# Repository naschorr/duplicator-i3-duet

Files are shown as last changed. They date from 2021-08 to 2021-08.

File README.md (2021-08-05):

# duplicator-i3-duet
Complete Duet 3 Mini 5+ based overhaul for the Duplicator i3 family of printers

Note that this repository is a work in progress, so some parts may not be compatible with the printer yet.

## Components
These are the required components for the upgraded printer, each section goes over it's own list of parts, printables, and tools.

- [duet case and mount assembly](assemblies/duet_case_and_mount_assembly.md)
- [extruder assembly](assemblies/extruder_assembly.md)
- [power supply dock and mount assembly](assemblies/power_supply_dock_and_mount_assembly.md)
- [x axis motor assembly](assemblies/x_axis_motor_assembly.md)
- [y axis carriage assembly](assemblies/y_axis_carriage_assembly.md)

## Required Tools
| Tool | Link | Notes |
| ---- | ---- | ----- |
| Terminal Crimper | [Amazon](https://smile.amazon.com/s?k=molex+jst+crimper) | Make sure it can do 26 gauge thru 12 gauge terminals
| Flush Cutter | [Amazon](https://smile.amazon.com/Hakko-CHP-170-Micro-Cutter/dp/B00FZPDG1K/) |
| Wire Stripper | [Amazon](https://smile.amazon.com/s?k=wire+stripper) |
| Power Drill |
| 1/8 Twist Drill Bit | [Amazon](https://smile.amazon.com/s?k=1%2F8+twist+drill) | This is for cleaning up a few 3D printed holes, so low quality is fine
| Heat Gun (or a lighter) | [Amazon](https://smile.amazon.com/s?k=heat+gun) | This is for heating up heatshrink tubing, so a lighter is totally fine
| Screw Driver Set | [Amazon](https://smile.amazon.com/Syntus-Precision-Screwdriver-Electronics-Cellphone/dp/B071PB4RPV) | Must contain a variety of Hex and Philips head drivers

## Wiring
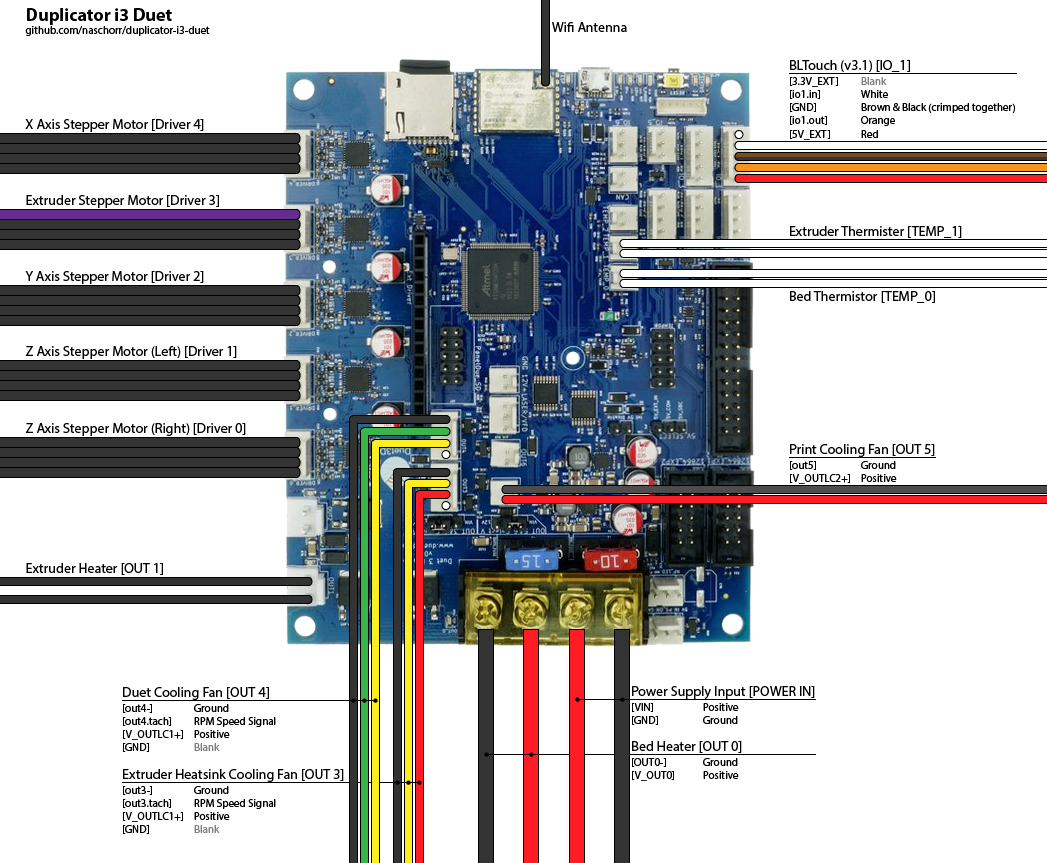
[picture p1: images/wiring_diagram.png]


## SD Card
The `*.g` files inside the [sd_card](sd_card/) directory contain the current state of configuration for the printer. Assuming an identical setup, these files can simply overwrite the data on your Duet's `System` directory.

## Additional Recommended Upgrades & Maintenance
- [Borosilicate Glass Bed](upgrades/borosilicate_glass_bed.md)
- [Z Braces](https://www.thingiverse.com/thing:921948)
- [Bed Levelling Thumbwheels](https://www.thingiverse.com/thing:1917422)
- [GT2 5mm Idler Pulleys](https://smile.amazon.com/gp/product/B01H3F8LUU)

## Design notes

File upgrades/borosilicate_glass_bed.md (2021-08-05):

# Borosilicate Glass Bed Upgrade

Upgrades the existing print surface to include a larger, flatter bed that makes the entire print volume available.

## Required Tools
| Tool | Link | Notes |
| ---- | ---- | ----- |
| Power Drill |
| Countersink Drill Bit | [Amazon](https://smile.amazon.com/gp/product/B0002EVG0C) | The aluminum of the bed is soft, so you can get a cheaper one if desired
| Goo Gone | [Amazon](https://smile.amazon.com/Goo-Gone-Adhesive-Remover-Spray/dp/B00S9YIQMS)  | The spray bottle isn't necessary, but it should make application easier
| Sharp Metal Spatula | | The Duplicator i3 should've already come with one

## Bill of Materials
| Item | Quantity | Link | Notes |
| ---- | --- | ---- | ----- |
| 235mm² Borosilicate Glass Bed | 1 | [Amazon](https://smile.amazon.com/gp/product/B07JKGNB6W)  |
| 200mm² 1mm Silicone Thermal Pad | 1 | [Amazon](https://smile.amazon.com/gp/product/B08YJNDLGM)  |
| M3 25mm Countersunk Machine Screw | 4 | Amazon
| M3 Locknuts | 4 | Amazon |
| Glass Bed Clips | 4 | [Amazon](https://smile.amazon.com/gp/product/B08W8NXMJC)  |

## Assembly
1. Remove the existing print surface, and if necessary scrape away any adhesive with the Goo Gone and a sharp spatula.
2. Remove the heated bed plate from the Y carriage. Making sure to remove the screws, washers, and springs.
3. Use the countersink drill bit to countersink the top of each of the screw holes. The countersink screws should sit very slightly proud of the heated bed's surface. Be careful not to remove too much material as the thin aluminum below the countersink can fail when tightening the screws down.
4. Reassemble the heated build plate
    - Place a M3 countersink screw through one of the bed's holes
    - Place one of the old washers on the screw, against the bottom of the bed
    - Tighten a M3 locknut on the screw until it touches the washer snugly. Don't over torque the nut as it will damage the bed.
    - Repeat for each of the four holes
5. Add a spring and a washer to each of the screws, and then lower the whole assembly back onto the Y carriage. Make sure all of the screws are properly aligned into their holes in the carriage without any binding.
6. Tighten the bed levelling thumbwheels/wingnuts onto each of the protruding screws below the Y carriage.
7. Apply the glass bed clips as necessary near each corner.
8. Update `config.g` to use the appropriate X and Y axis maxima.
9. Manually re-tram the bed, before performing a final mesh bed probe operation (`Control` > `Dashboard` > `Compensation & Calibration` > `Run Mesh Compensation (G29)`).
10. After the probing has completed, you can view the results in the height map viewer (`Control` > `Height Map`), assuming the height map plugin is enabled. Note that height maps must be activated, so that compensation can be applied. If you're using my configuration, then this is done for you.

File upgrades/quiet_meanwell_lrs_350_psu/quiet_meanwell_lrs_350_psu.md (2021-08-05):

# Quiet Meanwell LRS-350-12 Power Supply

Upgrades the default 12v power supply to a Meanwell LRS-350-12, with a larger, quieter fan. Note that this assembly uses the same chassis mount as the plain Meanwell LRS-350 power supply upgrade. This upgrade requires opening up the power supply, so obviously be careful and don't do anything dangerous while you're in there. If you're not comfortable with working around (potentially) charged capacitors then don't attempt this upgrade.

## Bill of Materials
| Item | Quantity | Link | Notes |
| ---- | --- | ---- | ----- |
| Meanwell LRS-350-12 Power Supply  | 1 | [Mouser](https://www.mouser.com/ProductDetail/709-LRS350-12) |
| Noctua NF-A9x14 PWM | 1 | [Amazon](https://smile.amazon.com/gp/product/B009NQM7V2/) | Alternatively, any 92x14mm fan will work here, I just like the performance and quietness of the Noctua.
| 4 Pin to 2 Pin Fan Adapter | 1 | [Amazon](https://smile.amazon.com/s?k=4+pin+to+2+pin+fan+adapter) | The Noctua NF-A4x10 FLX listed in the main bill of materials should come with a 3 pin to 2 pin adapter, which can be cut to allow a 4 pin header to connect. Note that I had to swap the order of the pins in the 2 pin end of the adapter. Alternatively you can purchase a new one.
| M3 6mm Socket Cap Machine Screws  | 4 | Amazon | If you've done the Z brace upgrade, then you likely have enough screws left over from that.
| M4 6mm Socket Cap Machine Screws  | 2 | Amazon | You can salvage these (non socket cap) from the printer's Y axis bearing block during the upgrade.
| M4 Washers | 2 | [Amazon](https://smile.amazon.com/gp/product/B07CG9J4NC) |
| 92mm Fan Filter Mesh | 1 | [Amazon](https://smile.amazon.com/ThreeBulls-Cooler-Filter-Dustproof-Computer/dp/B01N952K7P) | These are 120mm, but they're easier to find, useful elsewhere, and easy to cut to shape.
| Zip tie | 1 | [Amazon](https://smile.amazon.com/AmazonBasics-Multi-Purpose-Cable-Ties-200-Piece/dp/B087MKMSDY)  |

## Required Tools
| Tool | Link | Notes |
| ---- | ---- | ----- |
| Screw Driver Set  | [Amazon](https://smile.amazon.com/Syntus-Precision-Screwdriver-Electronics-Cellphone/dp/B071PB4RPV) | Must contain a variety of Hex and Phillips head drivers

## Printables
All items can be printed with a lower temperature filament, like PLA.
| STL | Quantity | Notes |
| --- | --- | ----- |
| duplicator i3 duet lrs 350 psu 92mm fan case.stl | 1 | This is the new outer case for the power supply, with a mounting solution for a 92x14mm fan.
| duplicator i3 duet lrs 350 psu 92mm fan dock.stl | 1 | This is the revised dock that the power supply (with case) slides into
| duplicator i3 duet lrs 350 psu 92mm fan clip.stl | 4 | These are the clips that screw into the outer case which hold the fan in place

## Assembly
Here's what the almost-completed 92mm fan case assembly should look like, with the fan, filter mesh (not seen), and fan clips installed into the fan case. All that's left to do is to screw the newly printed case and the original metal case together with the four original screws.

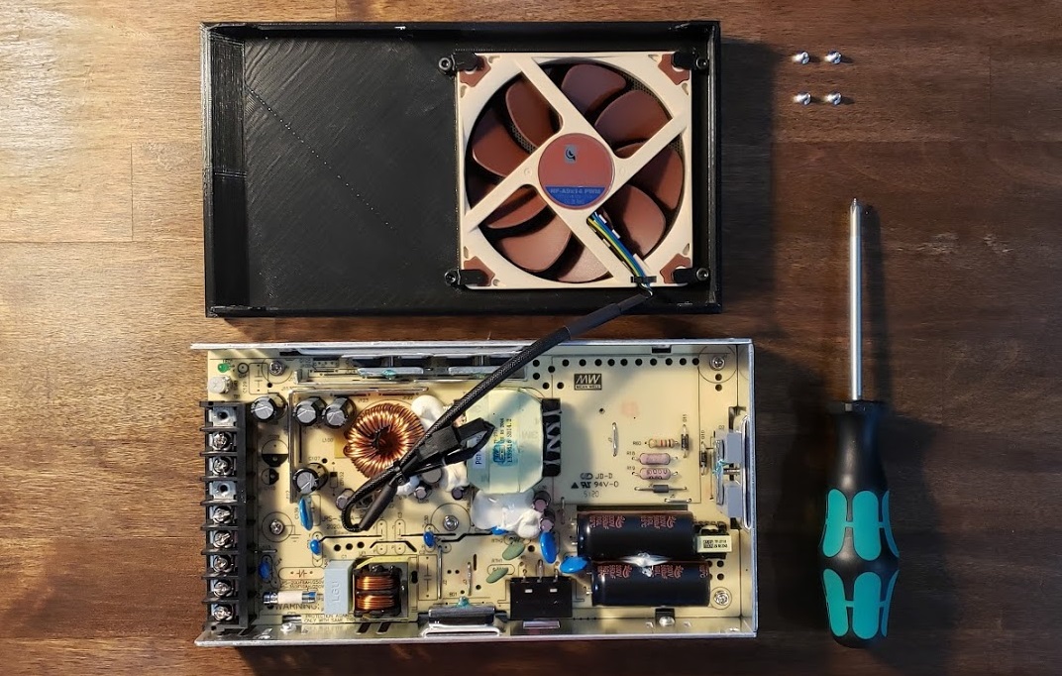
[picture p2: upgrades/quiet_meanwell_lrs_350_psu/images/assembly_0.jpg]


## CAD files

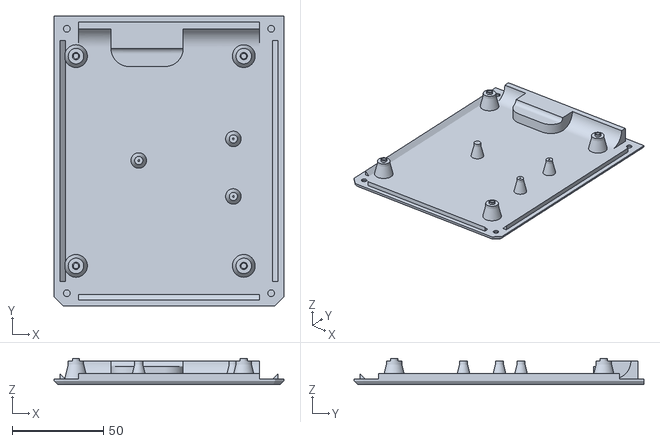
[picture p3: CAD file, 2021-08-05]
stls/duet_case_and_mount_assembly/duplicator i3 duet controller case back panel.stl
126.0 x 159.0 x 14.4

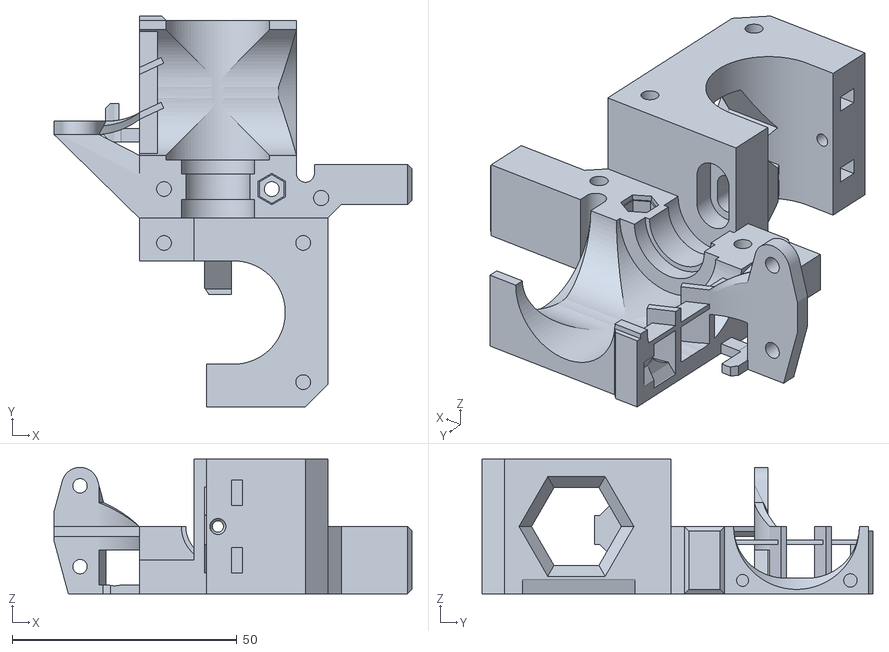
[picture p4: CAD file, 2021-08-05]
stls/extruder_assembly/duplicator i3 duet extruder body bltouch mount.stl
79.7 x 87.0 x 30.0

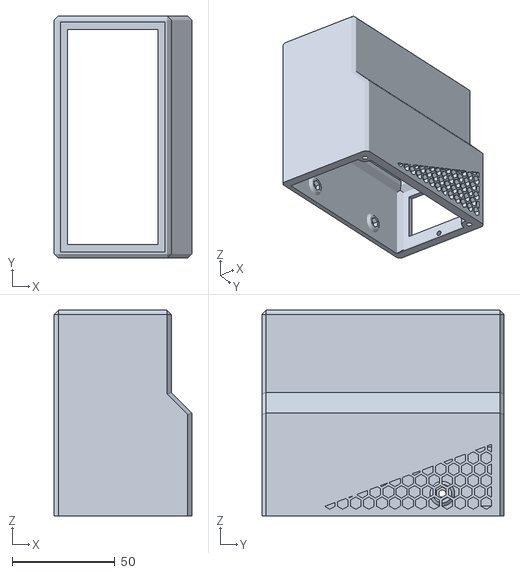
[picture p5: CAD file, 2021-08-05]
stls/power_supply_dock_and_mount_assembly/maker_select/duplicator i3 duet stock psu dock.stl
67.0 x 117.8 x 100.0

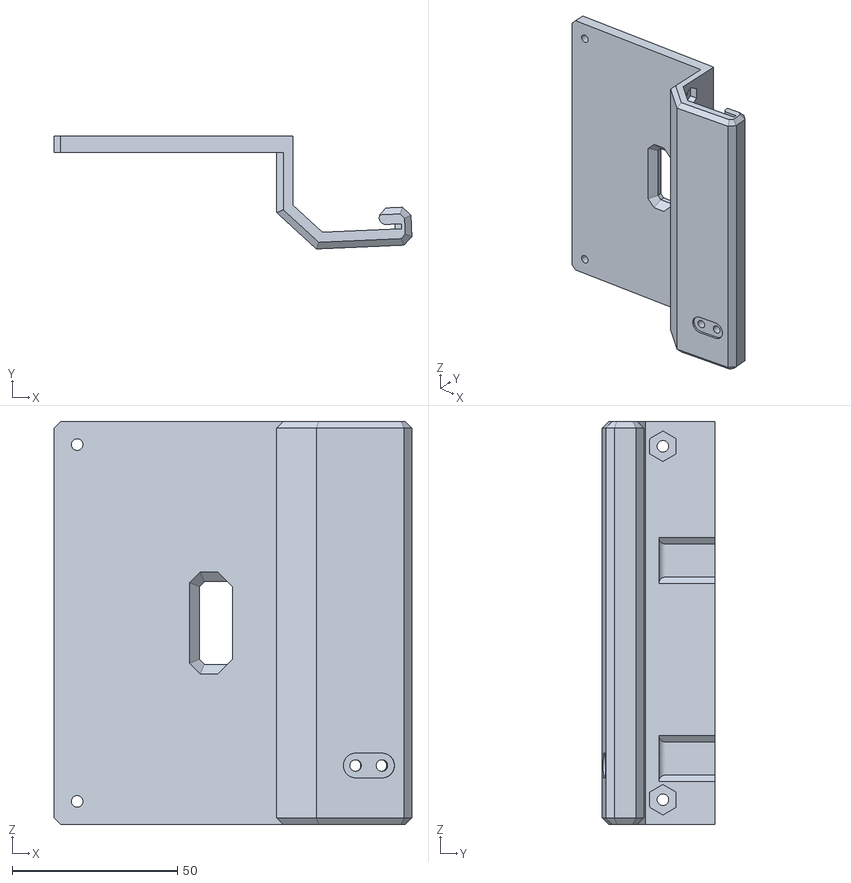
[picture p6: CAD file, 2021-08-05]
stls/power_supply_dock_and_mount_assembly/meanwell_lrs_350/duplicator i3 duet lrs 350 psu chassis mount.stl
108.3 x 34.2 x 122.0

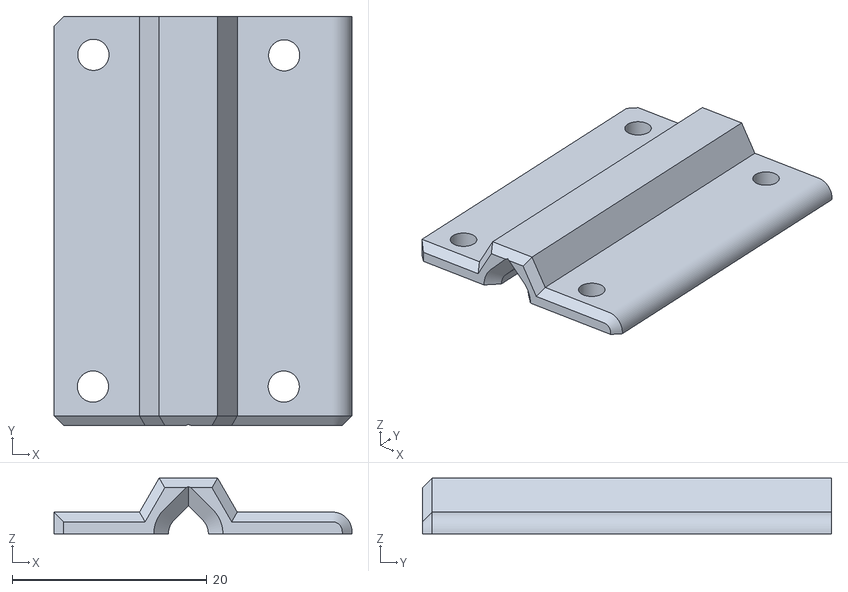
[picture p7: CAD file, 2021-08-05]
stls/x_axis_motor_assembly/duplicator i3 duet x motor ptfe outer clamp.stl
30.6 x 42.0 x 5.75

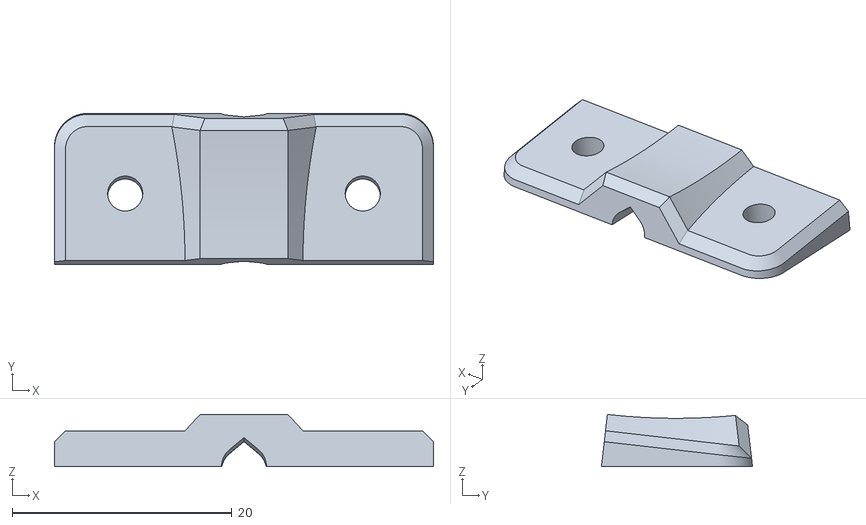
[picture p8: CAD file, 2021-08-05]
stls/y_axis_carriage_assembly/duplicator i3 duet y carriage bearing block ptfe angled clamp.stl
34.5 x 13.8 x 4.75

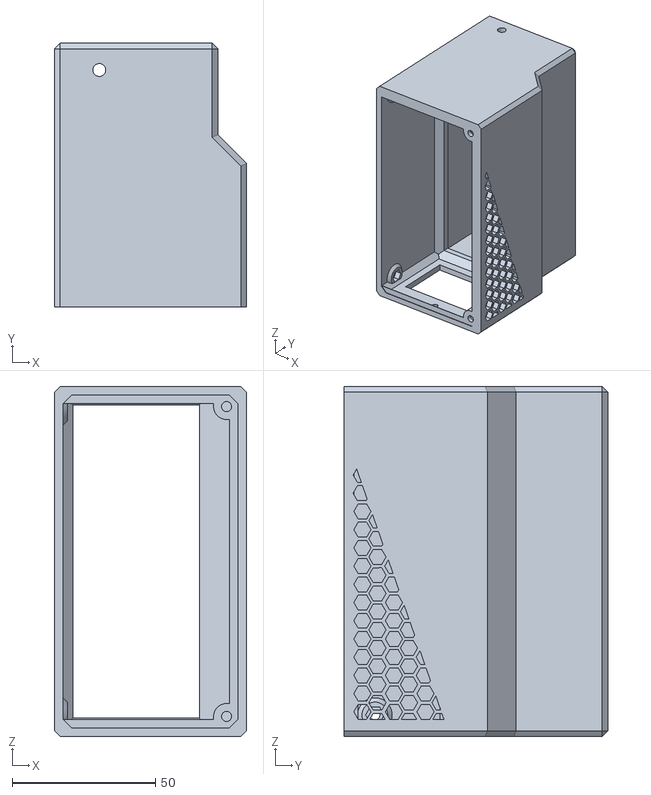
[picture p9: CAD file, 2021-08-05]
upgrades/quiet_meanwell_lrs_350_psu/duplicator i3 duet lrs 350 psu 92mm fan dock.stl
67.0 x 92.0 x 122.0

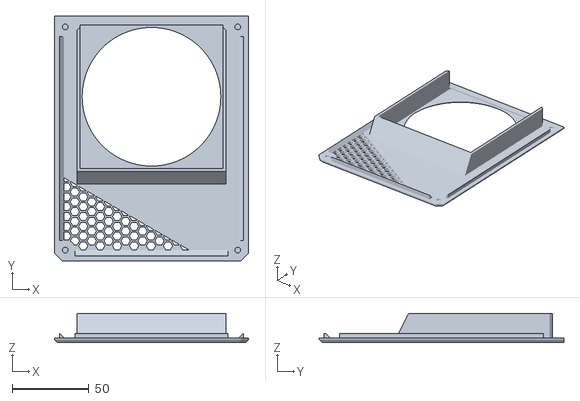
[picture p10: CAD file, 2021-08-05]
stls/duet_case_and_mount_assembly/duplicator i3 duet controller case front panel.stl
126.0 x 159.0 x 19.0

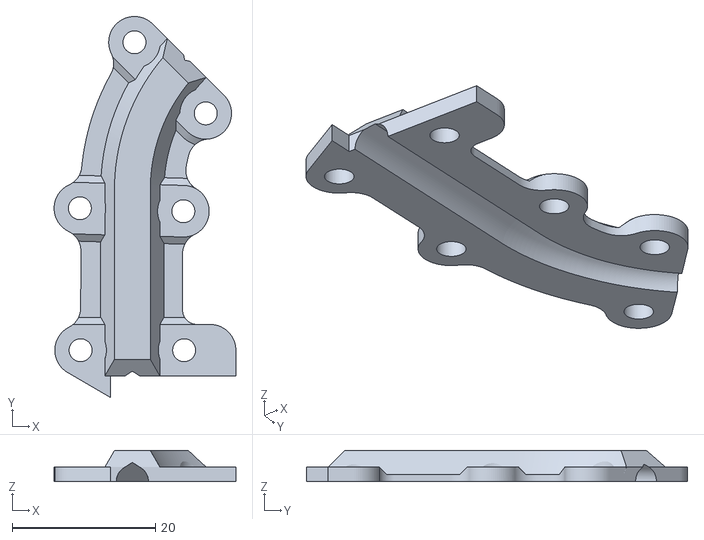
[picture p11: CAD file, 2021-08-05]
stls/extruder_assembly/duplicator i3 duet extruder x carriage ptfe clamp top.stl
25.4 x 53.2 x 4.33

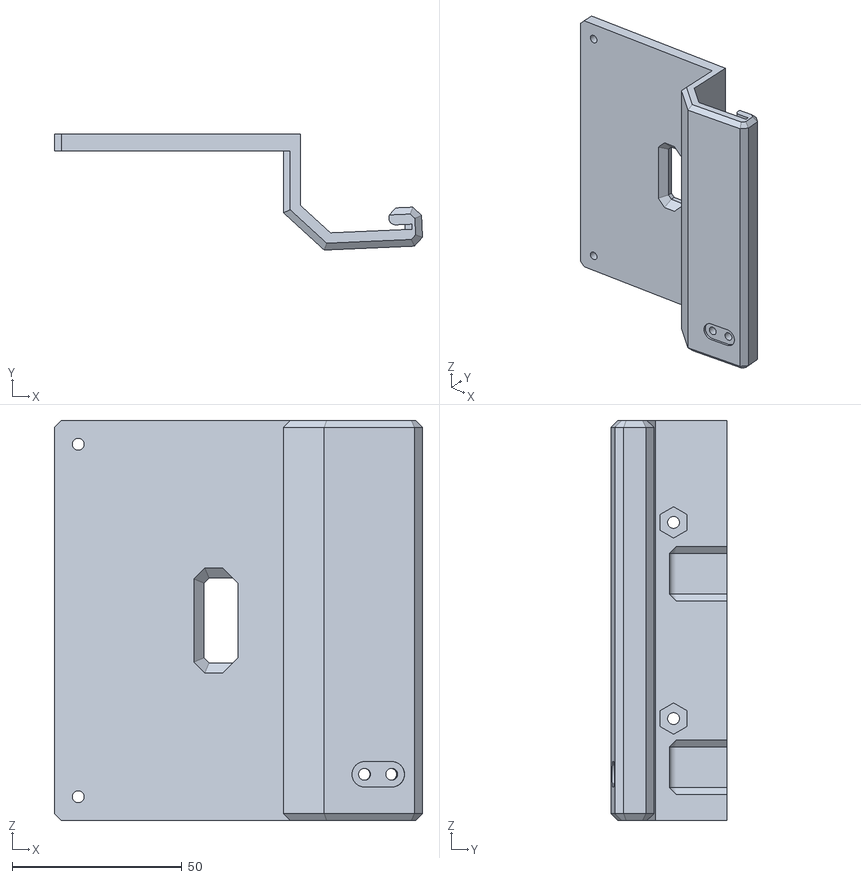
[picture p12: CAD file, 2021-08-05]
stls/power_supply_dock_and_mount_assembly/maker_select/duplicator i3 duet stock psu chassis mount.stl
108.3 x 34.2 x 117.8

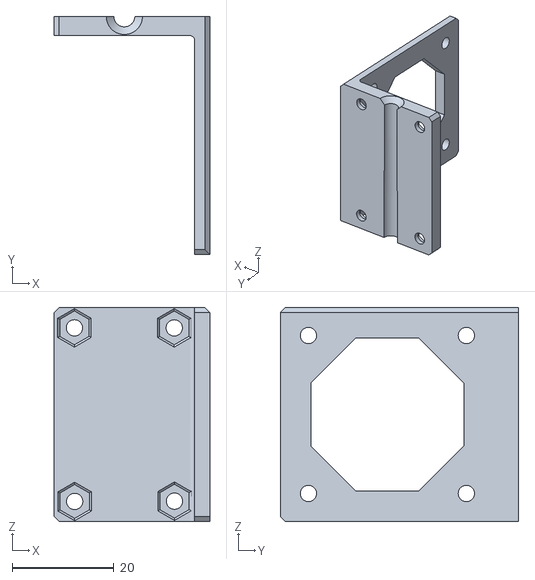
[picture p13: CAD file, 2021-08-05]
stls/x_axis_motor_assembly/duplicator i3 duet x motor ptfe inner clamp.stl
30.6 x 46.8 x 42.0

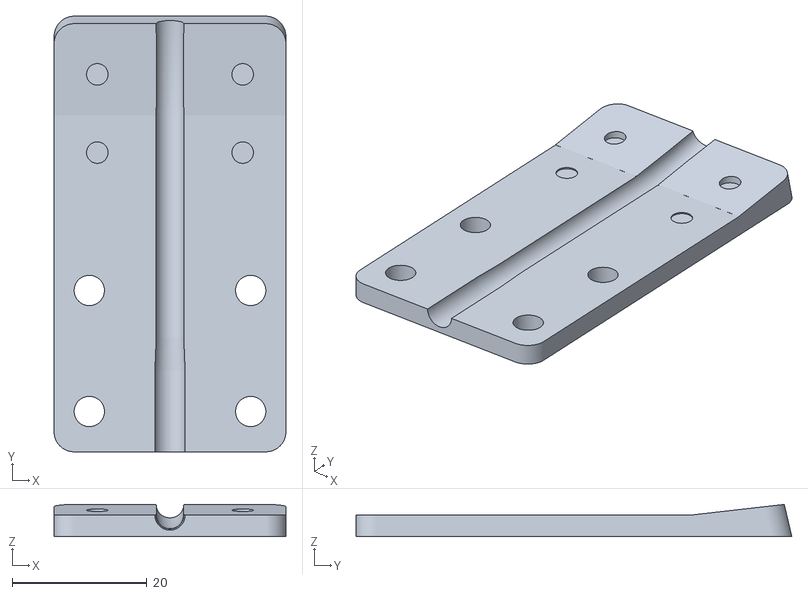
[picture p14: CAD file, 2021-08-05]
stls/y_axis_carriage_assembly/duplicator i3 duet y carriage bearing block ptfe lower clamp.stl
34.5 x 64.8 x 4.78

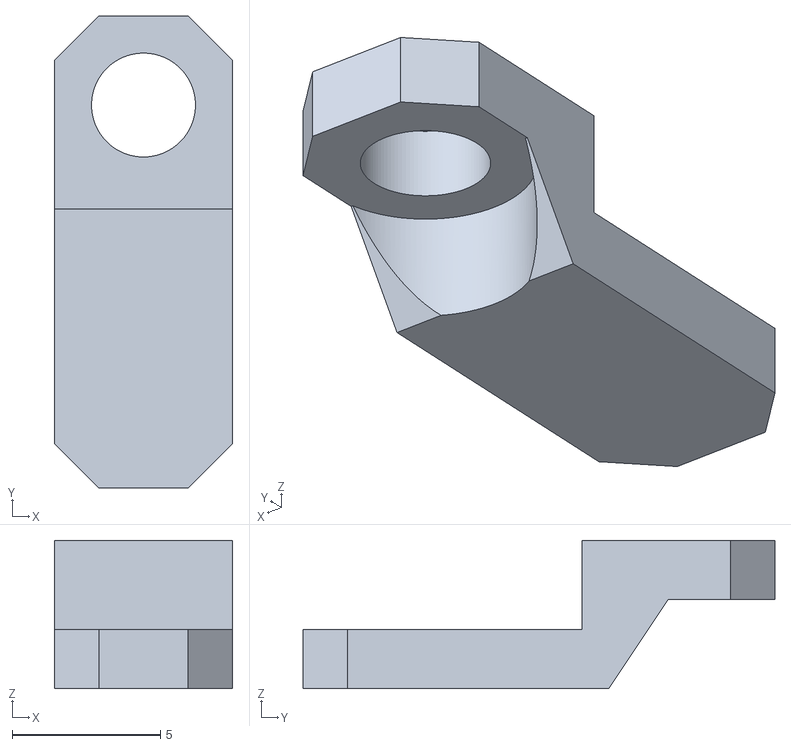
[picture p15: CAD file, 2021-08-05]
upgrades/quiet_meanwell_lrs_350_psu/duplicator i3 duet lrs 350 psu 92mm fan clip.stl
6.00 x 15.9 x 5.00

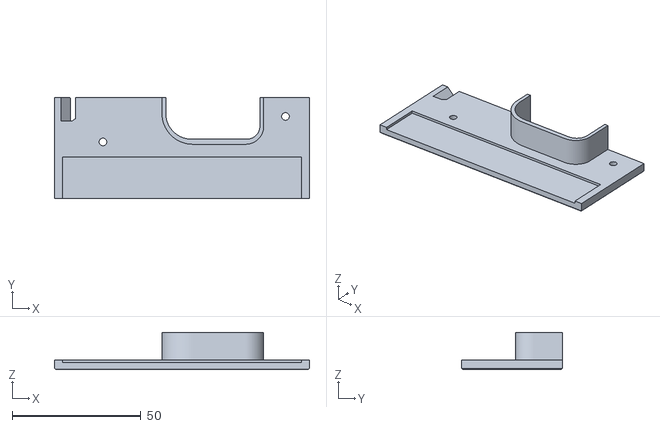
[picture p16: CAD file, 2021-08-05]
stls/duet_case_and_mount_assembly/duplicator i3 duet controller case fan rack.stl
99.2 x 39.4 x 14.5

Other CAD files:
stls/power_supply_dock_and_mount_assembly/meanwell_lrs_350/duplicator i3 duet lrs 350 psu dock.stl
stls/extruder_assembly/prusa i3 mk2 extruder cover.stl
stls/y_axis_carriage_assembly/duplicator i3 duet y carriage bearing block ptfe upper clamp.stl
upgrades/quiet_meanwell_lrs_350_psu/duplicator i3 duet lrs 350 psu 92mm fan case.stl
stls/duet_case_and_mount_assembly/duplicator i3 duet controller case cable lock.stl
stls/duet_case_and_mount_assembly/duplicator i3 duet controller case chassis mount.stl
stls/duet_case_and_mount_assembly/duplicator i3 duet controller case left fan bracket.stl
stls/duet_case_and_mount_assembly/duplicator i3 duet controller case right fan bracket.stl
stls/duet_case_and_mount_assembly/duplicator i3 duet controller case sides.stl
stls/extruder_assembly/duplicator i3 duet extruder body 30mm to 40mm fan adapter.stl
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

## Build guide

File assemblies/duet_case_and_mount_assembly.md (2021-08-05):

# Duet Case and Mount Assembly

## Printables
All of these files can be printed in any filament type you'd like.

| STL | Quantity |
| --- | --- |
| duplicator i3 duet controller case chassis mount.stl | 1 | 
| duplicator i3 duet controller case back panel.stl | 1 | 
| duplicator i3 duet controller case sides.stl | 1 | 
| duplicator i3 duet controller case cable lock.stl | 3 | 
| duplicator i3 duet controller case fan rack.stl | 1 | 
| duplicator i3 duet controller case left fan bracket.stl | 1 | 
| duplicator i3 duet controller case right fan bracket.stl  | 1 | 
| duplicator i3 duet controller case front panel.stl | 1 | 

## Required Tools
| Tool | Link | Notes |
| ---- | ---- | ----- |
| Terminal Crimper | [Amazon](https://smile.amazon.com/s?k=molex+jst+crimper) | Make sure it can do 26 gauge thru 12 gauge terminals
| Flush Cutter | [Amazon](https://smile.amazon.com/Hakko-CHP-170-Micro-Cutter/dp/B00FZPDG1K/) |
| Wire Stripper | [Amazon](https://smile.amazon.com/s?k=wire+stripper) |
| Power Drill | 
| 1/8 Twist Drill Bit | [Amazon](https://smile.amazon.com/s?k=1%2F8+twist+drill) | This is for cleaning up a few 3D printed holes, so low quality is fine
| Screw Driver Set | [Amazon](https://smile.amazon.com/Syntus-Precision-Screwdriver-Electronics-Cellphone/dp/B071PB4RPV) | Must contain a variety of Hex and Philips head drivers

## Bill of Materials
Note that several of the links are to parts assortments, and a single assortment should cover all of the parts of that type. Obviously, you can also source parts elsewhere if desired, the linked ones are just a convenient option.

| Item | Quantity | Link | Notes |
| ---- | --- | ---- | ----- |
| Duet 3 Mini 5+ Wifi | 1 | [Filastruder](https://www.filastruder.com/collections/electronics/products/duet-3-mini-5) | My STLs don't allow for the ethernet cable to pass through them anywhere, so you must get the Wifi version. |
| Noctua NF-A9x14 PWM | 1 | [Amazon](https://smile.amazon.com/gp/product/B009NQM7V2/) | Alternatively, any 92x14mm fan will work here, I just like the performance and quietness of the Noctua. |
| 92mm Fan Filter Mesh | 1 | [Amazon](https://smile.amazon.com/ThreeBulls-Cooler-Filter-Dustproof-Computer/dp/B01N952K7P) | These are 120mm, but they're easier to find, useful elsewhere, and easy to cut to shape.
| M3 6mm Socket Cap Machine Screws | 6 | Amazon | If you've done the Z brace upgrade, then you likely have enough screws left over from that.
| M3 10mm Socket Cap Machine Screws | 23 | Amazon |
| M3 Washers | 24 | [Amazon](https://smile.amazon.com/gp/product/B07CG9J4NC) |
| M3 Hex Nuts | 6 | Amazon |
| M3 Square Nuts | 12 | Amazon |
| Zip ties | 3 | [Amazon](https://smile.amazon.com/gp/product/B01M06HTVH) | 4 inch zip ties are fine here.

## Images
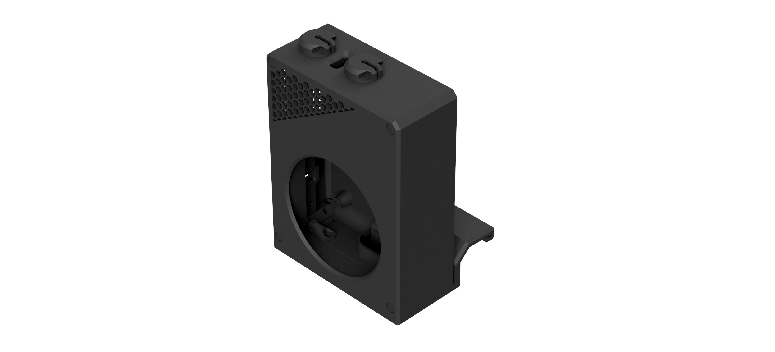
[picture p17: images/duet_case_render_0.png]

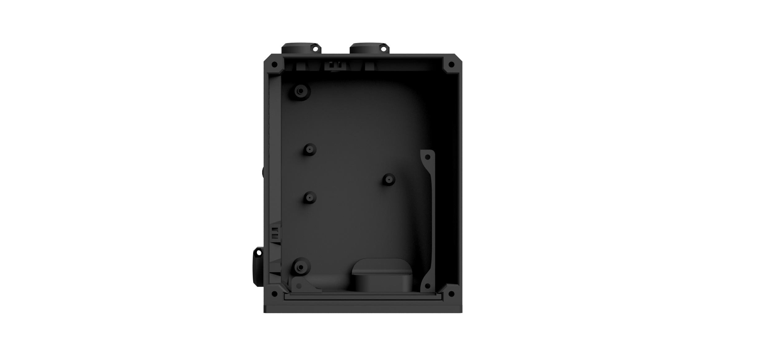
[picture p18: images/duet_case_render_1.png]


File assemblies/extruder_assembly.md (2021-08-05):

# Extruder Assembly

## Printables
All of these files should be printed in a thermally resistant filament, like PETG.

| STL | Quantity | Notes |
| --- | --- | ----- |
| duplicator i3 duet extruder body bltouch mount.stl | 1 | This is essentially just a normal Prusa i3 MK2 extruder body, but with a BLTouch mount grafted onto it
| duplicator i3 duet extruder body 30mm to 40mm fan adapter.stl | 1 | This will adapt the 30mm fan attachment point to allow a 40mm fan to be used instead
| duplicator i3 duet extruder x carriage ptfe clamp top.stl | 1 | 
| duplicator i3 duet extruder x carriage ptfe clamp bottom.stl  | 1 | 
| duplicator i3 duet extruder idler shaft.stl | 1 | WIP
| duplicator i3 duet extruder idler washer.stl | 2 | WIP
| prusa i3 mk2 extruder cover.stl | 1 | This is literally just the official part from Prusa, included here for convenience
| prusa i3 mk2 extruder idler.stl | 1 | This is literally just the official part from Prusa, included here for convenience
| prusa i3 mk2 x carriage.stl | 1 | This is literally just the official part from Prusa, included here for convenience

## Required Tools
| Tool | Link | Notes |
| ---- | ---- | ----- |
| Terminal Crimper | [Amazon](https://smile.amazon.com/s?k=molex+jst+crimper) | Make sure it can do 26 gauge thru 12 gauge terminals
| Flush Cutter | [Amazon](https://smile.amazon.com/Hakko-CHP-170-Micro-Cutter/dp/B00FZPDG1K/) |
| Wire Stripper | [Amazon](https://smile.amazon.com/s?k=wire+stripper) |
| Power Drill | 
| 1/8 Twist Drill Bit | [Amazon](https://smile.amazon.com/s?k=1%2F8+twist+drill) | This is for cleaning up a few 3D printed holes, so low quality is fine
| Heat Gun (or a lighter) | [Amazon](https://smile.amazon.com/s?k=heat+gun) 
| Screw Driver Set | [Amazon](https://smile.amazon.com/Syntus-Precision-Screwdriver-Electronics-Cellphone/dp/B071PB4RPV) | Must contain a variety of Hex head drivers

## Bill of Materials
Note that several of the links are to parts assortments, and a single assortment should cover all of the parts of that type. Obviously, you can also source parts elsewhere if desired, the linked ones are just a convenient option.

| Item | Quantity | Link | Notes |
| ---- | --- | ---- | ----- |
| E3D V6 Hotend | 1 | [Filastruder](https://www.filastruder.com/products/all-metal-e3d-v6-hotend?variant=747155309) |
| Extruder Drive Gear | 1 | [Filastruder](https://www.filastruder.com/collections/e3d-spare-parts-and-accessories/products/hobb-goblin-5mm-id-drive-gear)
| BLTouch (v3.1 or greater) | 1 | [Filastruder](https://www.filastruder.com/collections/electronics/products/bltouch-automatic-bed-leveling-probe)
| BLTouch Extension Cable | 1 meter | [Filastruder](https://www.filastruder.com/products/bltouch-1000mm-cable)
| Noctua NF-A4x10 FLX | 1 | [Amazon](https://smile.amazon.com/gp/product/B009NQLT0M/) | Alternatively, any 40x10mm fan will work here, I just like the performance and quietness of the Noctua. |
| Sunon 5015 Blower Fan | 1 | [Mouser](https://www.mouser.com/ProductDetail/369-MF50151VXB00UA99) |
| PTFE Tubing 2mm ID | 750mm | [Filastruder](https://www.filastruder.com/collections/e3d-spare-parts-and-accessories/products/ptfe-tubing?variant=485332121) | This is an approximation, purchase all PTFE tubing in a single length and cut to size.
| 26 Gauge Wire | 7 meters  | Mouser | This is for the heatsink fan, the part cooler blower, and the extruder's thermistor
| 22 Gauge Wire | 2 meters  | Mouser | This is for the extruder heater itself.
| 625 Bearing | 1 | Amazon
| Extruder Spring | 2 | DIY | I ended up pulling the springs out of a couple clicky pens, and stretching them out a bit. That said, these can probably be found on ebay or aliexpress with enough persistence.
| M3 6mm Socket Cap Machine Screws | 6 | Amazon | If you've done the Z brace upgrade, then you likely have enough screws left over from that.
| M3 18mm Socket Cap Machine Screws | 2 | Amazon
| M3 20mm Socket Cap Machine Screws | 3 | Amazon
| M3 25mm Socket Cap Machine Screws | 1 | Amazon | I believe this one (used in step 7 of Prusa's assembly guide) can be replaced with a M3 30mm machine screw and another M3 washer.
| M3 30mm Socket Cap Machine Screws | 3 | Amazon
| M3 40mm Socket Cap Machine Screws | 4 | Amazon
| M3 Washers | 10 | [Amazon](https://smile.amazon.com/gp/product/B07CG9J4NC)
| M3 Hex Nuts | 10 | Amazon
| M3 Square Nuts | 4 | Amazon
| Zip ties | 8+ | [Amazon](https://smile.amazon.com/gp/product/B01M06HTVH) | 4 inch zip ties are fine here.

## Assembly
You can follow the [official Prusa i3 MK2 extruder assembly guide](https://help.prusa3d.com/en/guide/5-extruder-assembly_82960) for this one. Almost all extruder parts for this upgrade are derived from Prusa's designs.

## Images
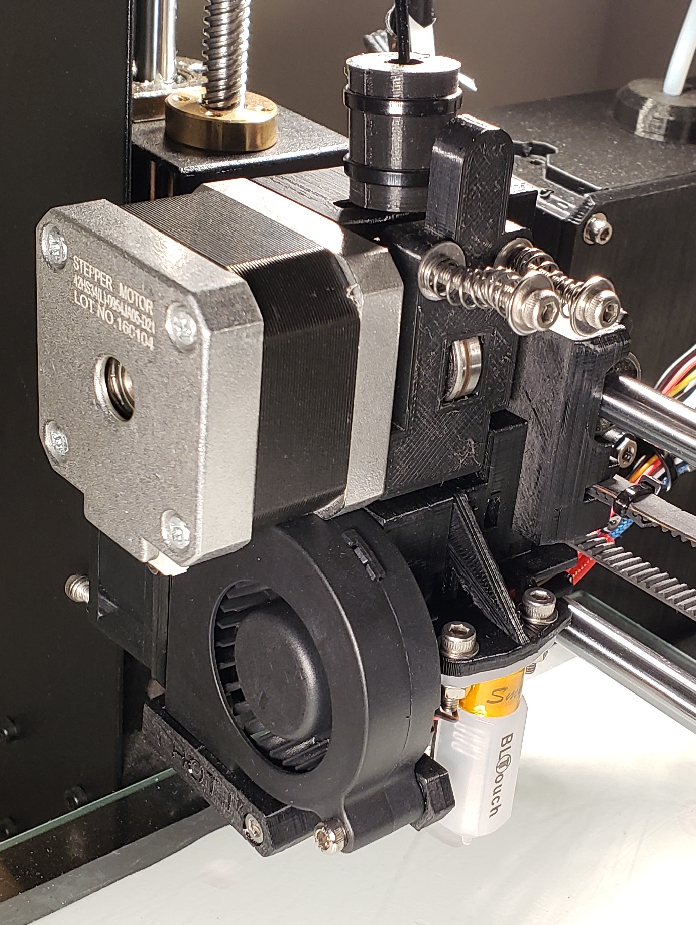
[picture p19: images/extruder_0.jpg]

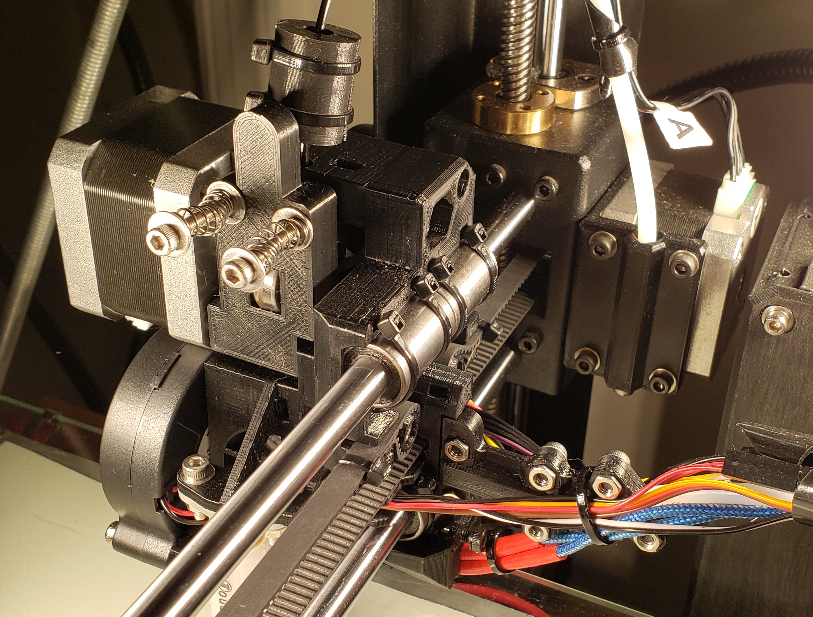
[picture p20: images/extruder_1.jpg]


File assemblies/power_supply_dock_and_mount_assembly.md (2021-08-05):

# Power Supply Dock and Mount Assembly

## Multiple Choice

There's three different ways to approach the power supply question.

### Default Maker Select Power Supply
This is the budget option, and will reuse the 12v supply that came with your Duplicator i3.

All STLs only need to be printed once, and can be printed out of any filament type you'd like.

| STL |
| --- |
| duplicator i3 duet stock psu chassis mount.stl    |
| duplicator i3 duet stock psu dock.stl             |

### Normal Meanwell LRS-350-12 Power Supply
Having issues with the stock power supply? Upgrade it to a proper unit from Meanwell.

All STLs only need to be printed once, and can be printed out of any filament type you'd like.

| STL |
| --- |
| duplicator i3 duet lrs 350 psu chassis mount.stl  |
| duplicator i3 duet lrs 350 psu dock.stl           |

### Quiet Meanwell LRS-350-12 Power Supply
This is the ultimate option, which takes that same Meanwell unit and upgrades the case to house a significantly larger fan. The fan makes this thing nearly silent, and ideal if the printer sits in the same room as you do. I absolutely recommend this option.

Take a look at the separate upgrade page [here](../upgrades/quiet_meanwell_lrs_350_psu/quiet_meanwell_lrs_350_psu.md) that goes into greater detail.

## Required Tools
| Tool | Link | Notes |
| ---- | ---- | ----- |
| Terminal Crimper | [Amazon](https://smile.amazon.com/s?k=molex+jst+crimper) | Make sure it can do 26 gauge thru 12 gauge terminals
| Flush Cutter | [Amazon](https://smile.amazon.com/Hakko-CHP-170-Micro-Cutter/dp/B00FZPDG1K/) |
| Wire Stripper | [Amazon](https://smile.amazon.com/s?k=wire+stripper) |
| Heat Gun (or a lighter) | [Amazon](https://smile.amazon.com/s?k=heat+gun) 
| Screw Driver Set | [Amazon](https://smile.amazon.com/Syntus-Precision-Screwdriver-Electronics-Cellphone/dp/B071PB4RPV) | Must contain a variety of Hex and Philips head drivers

## Bill of Materials
Note that several of the links are to parts assortments, and a single assortment should cover all of the parts of that type. Obviously, you can also source parts elsewhere if desired, the linked ones are just a convenient option.

| Item | Quantity | Link | Notes |
| ---- | --- | ---- | ----- |
| 12 Gauge Wire | 2 meters  | [Mouser](https://www.mouser.com/ProductDetail/TE-Connectivity-Raychem/44A0111-12-0CS448?qs=pLY5GE0xrmJhn6WhPS46fA%3D%3D) | 12 gauge is a bit overkill, but safety is worth it
| 12 Gauge Spade Terminal | 2 | [Mouser](https://www.mouser.com/ProductDetail/Molex/19131-0004?qs=sLlYHtrnUedrBRMIT5hiJw%3D%3D) | These might need some slight filing down to fit into the terminal block
| M3 6mm Socket Cap Machine Screws | 2 | Amazon | If you've done the Z brace upgrade, then you likely have enough screws left over from that.
| M3 10mm Socket Cap Machine Screws | 6 | Amazon |
| M3 Washers | 6 | [Amazon](https://smile.amazon.com/gp/product/B07CG9J4NC) |
| M3 Hex Nuts | 6 | Amazon |

## Images
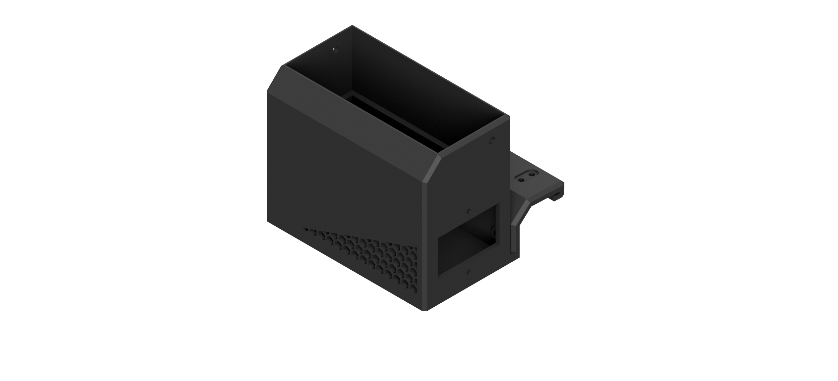
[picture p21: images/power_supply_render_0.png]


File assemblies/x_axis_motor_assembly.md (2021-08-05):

# X Axis Motor Assembly

## Printables
All STLs only need to be printed once, and in any filament type you'd like.

| STL |
| --- |
| duplicator i3 duet x motor ptfe inner clamp.stl   | 
| duplicator i3 duet x motor ptfe outer clamp.stl   | 

## Required Tools
| Tool | Link | Notes |
| ---- | ---- | ----- |
| Screw Driver Set | [Amazon](https://smile.amazon.com/Syntus-Precision-Screwdriver-Electronics-Cellphone/dp/B071PB4RPV) | Must contain a variety of Hex head drivers

## Bill of Materials
Note that several of the links are to parts assortments, and a single assortment should cover all of the parts of that type. Obviously, you can also source parts elsewhere if desired, the linked ones are just a convenient option.

| Item | Quantity | Link | Notes |
| ---- | --- | ---- | ----- |
| PTFE Tubing 2mm ID | 500 mm | [Filastruder](https://www.filastruder.com/collections/e3d-spare-parts-and-accessories/products/ptfe-tubing?variant=485332121) | This is an approximation, purchase all PTFE tubing in a single length and cut to size.
| M3 6mm Socket Cap Machine Screws | 4 | Amazon | If you've done the Z brace upgrade, then you likely have enough screws left over from that.
| M3 Washers | 4 | [Amazon](https://smile.amazon.com/gp/product/B07CG9J4NC) |
| M3 Hex Nuts | 4 | Amazon 

## Images
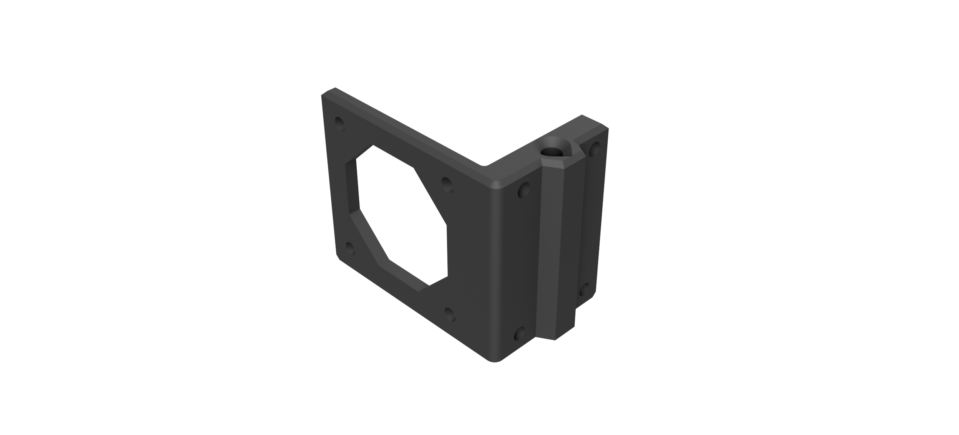
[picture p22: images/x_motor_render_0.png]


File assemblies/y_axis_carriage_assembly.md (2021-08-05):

# Y Axis Carriage Assembly

## Printables
All STLs only need to be printed once. These should be printed out of a filament that's more tolerant of higher temperatures, like PETG.

| STL |
| --- |
| duplicator i3 duet y carriage bearing block ptfe angled clamp.stl | 
| duplicator i3 duet y carriage bearing block ptfe lower clamp.stl  | 
| duplicator i3 duet y carriage bearing block ptfe upper clamp.stl  | 

## Required Tools
| Tool | Link | Notes |
| ---- | ---- | ----- |
| Power Drill |
| 1/8 Twist Drill Bit | [Amazon](https://smile.amazon.com/s?k=1%2F8+twist+drill) | This is for cleaning up a few 3D printed holes, so low quality is fine
| Screw Driver Set | [Amazon](https://smile.amazon.com/Syntus-Precision-Screwdriver-Electronics-Cellphone/dp/B071PB4RPV) | Must contain a variety of Hex head drivers

## Bill of Materials
Note that several of the links are to parts assortments, and a single assortment should cover all of the parts of that type. Obviously, you can also source parts elsewhere if desired, the linked ones are just a convenient option.

| Item | Quantity | Link | Notes |
| ---- | --- | ---- | ----- |
| PTFE Tubing 2mm ID | 500 mm | [Filastruder](https://www.filastruder.com/collections/e3d-spare-parts-and-accessories/products/ptfe-tubing?variant=485332121) | This is an approximation, purchase all PTFE tubing in a single length and cut to size.
| M3 6mm Socket Cap Machine Screws | 4 | Amazon
| M3 Washers | 4 | [Amazon](https://smile.amazon.com/gp/product/B07CG9J4NC) |
| M3 Hex Nuts | 4 | Amazon
| M4 12mm Socket Cap Machine Screws | 4 | Amazon | You can salvage these from the printer's X carriage bearing block (I could be wrong, as I had upgraded to a Prusa i3 MK2 style X axis/extruder assembly years before this)
| M4 Washers | 4 | [Amazon](https://smile.amazon.com/gp/product/B07CG9J4NC) 

## Images
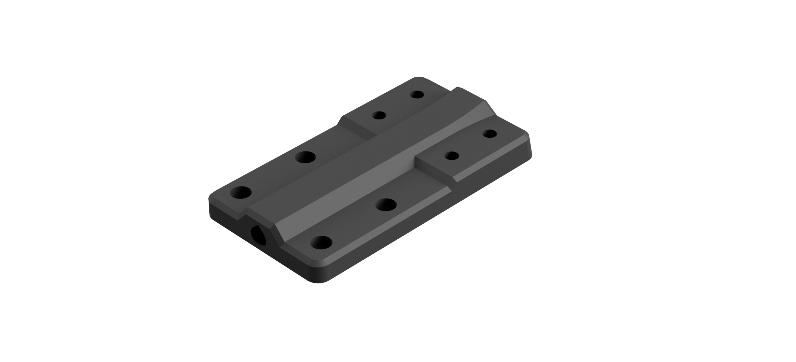
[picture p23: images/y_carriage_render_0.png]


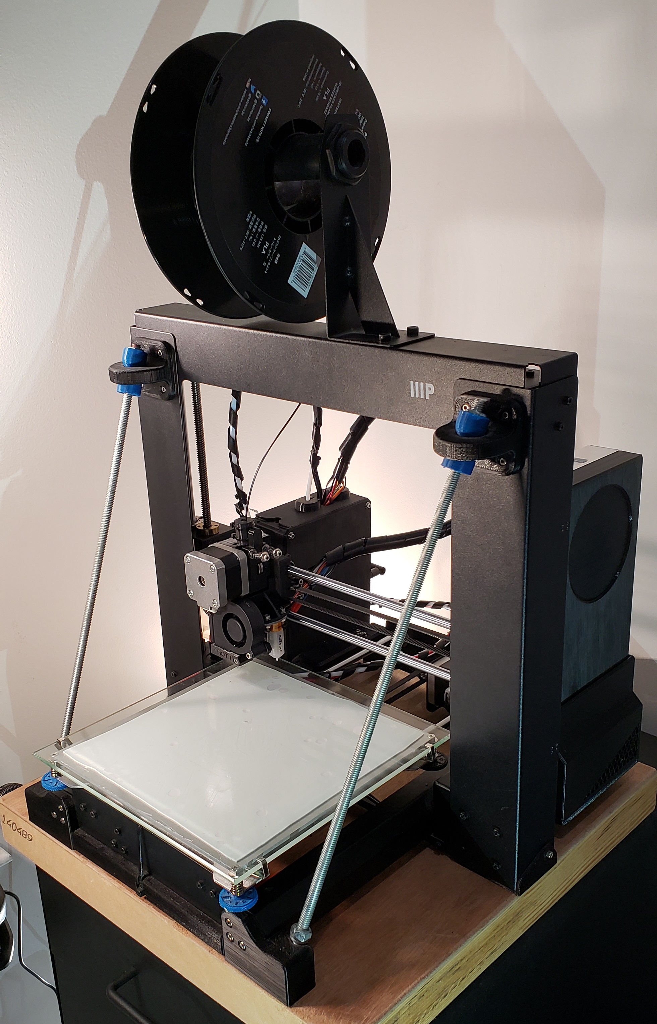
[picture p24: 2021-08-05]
images/printer.jpg

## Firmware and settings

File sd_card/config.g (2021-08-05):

; Configuration file for Duet 3 Mini 5+ (firmware version 3)
; executed by the firmware on start-up

; General preferences
G90                                                   ; send absolute coordinates...
M83                                                   ; ...but relative extruder moves
M550 P"Duplicator i3 Duet"                            ; set printer name

; Network
M552 S1                                               ; enable network
M586 P0 S1                                            ; enable HTTP
M586 P1 S0                                            ; disable FTP
M586 P2 S0                                            ; disable Telnet

; Drives
M569 P0.0 S1                                          ; physical drive 0.0 goes backwards   (Right Z axis motor)
M569 P0.1 S1                                          ; physical drive 0.1 goes backwards   (Left Z axis motor)
M569 P0.2 S0                                   		  ; physical drive 0.2 goes forwards    (Y axis motor)
M569 P0.3 S0                                          ; physical drive 0.3 goes forwards    (Extruder motor)
M569 P0.4 S1                                      	  ; physical drive 0.4 goes backwards   (X axis motor)
M584 X0.4 Y0.2 Z0.0:0.1 E0.3                          ; set drive mapping
M350 X128 Y128 Z128 I0                                ; configure microstepping without interpolation
M350 E16 I1                                           ; configure microstepping with interpolation
M92 X640.00 Y640.00 Z3200.00 E161.6                   ; set steps per mm
M566 X900.00 Y900.00 Z12.00 E120.00                   ; set maximum instantaneous speed changes (mm/min)
M203 X12000.00 Y12000.00 Z1200.00 E3000.00            ; set maximum speeds (mm/min)
M201 X800.00 Y800.00 Z80.00 E5000.00               	  ; set accelerations (mm/s^2)
M906 X855 Y855 Z855 E600 I30                          ; set motor currents (mA) and motor idle factor in per cent. See http://www.hacking3d.com/2016/05/wanhao-duplicator-i3-v2-stepper-tuning.html. Lowered extruder motor current for heat mitigation.
M84 S30                                               ; Set idle timeout

; Axis Limits
M208 X0 Y0 Z0 S1                                      ; set axis minima
; M208 X200 Y210 Z145 S0                              ; Axis maxima with stock bed
M208 X200 Y220 Z145 S0                                ; Axis maxima with the borosilicate glass bed upgrade (see README.md)

; Geometry
M669 K0												  ; Cartesian
M671 X-45:245 Y0:0 						  			  ; Set Z leadscrew positions (-15,0) and (100,0)

; Endstops
M574 X1 S3                                            ; configure sensorless endstop for low end on X
M574 Y1 S3                                            ; configure sensorless endstop for low end on Y
M574 Z1 S2                                            ; configure Z-probe endstop for low end on Z

; Stallguard
M915 X S3 F0 H234 R0
M915 Y S3 F0 H234 R0								  ; Slightly less sensitive Y axis stall detection, as it would tend to trigger too early without it

; BLTouch Z-Probe
M950 S0 C"io1.out"                                    ; create servo pin 0 for BLTouch
M558 P9 C"^io1.in" H5 F6000 T6000                     ; set Z probe type to bltouch and the dive height + speeds    F120 normally
G31 P500 X30.698 Y0 Z3.45                             ; set Z probe trigger value, offset and trigger height
M557 X32:178 Y32:188 S33.6:37.6                       ; define mesh grid

; Heaters
M308 S0 P"temp0" Y"thermistor" T100000 B3988          ; configure sensor 0 as thermistor on pin temp0
M950 H0 C"out0" T0                                    ; create bed heater output on out0 and map it to sensor 0
M307 H0 R0.279 C579.1 D3.15 S1.00 V12.1 B0			  ; Bed heater configuration with Borosilicate glass bed, Meanwell LRS 350, and disable bang-bang heating. Make sure to run "M303 H0 S60" to tune this properly.
M140 H0                                               ; map heated bed to heater 0
M143 H0 S120                                          ; set temperature limit for heater 0 to 120C
M308 S1 P"temp1" Y"thermistor" T100000 B4725 C7.06e-8 ; configure sensor 1 as thermistor on pin temp1
M950 H1 C"out1" T1                                    ; create nozzle heater output on out1 and map it to sensor 1
M307 H1 B0 S1.00                                      ; disable bang-bang mode for heater and set PWM limit
M143 H1 S280                                          ; set temperature limit for heater 1 to 280C

; Fans
M950 F0 C"out5" Q500                         	      ; Create fan 0 on pin out5 and set its frequency. Per the wiki, this will be the Print Cooling Fan.
M106 P0 C"Print Fan" S0 X0.75 H-1                  	  ; Set fan speed to 0, and disable thermostatic control, as printable gcode will control this. Limit speed to 75% of full as this is a beefy 5.4 cfm Sunon fan.
M950 F1 C"out3" Q25000								  ; Create fan 1 on pin out3 and set its frequency. Per the wiki, this will be the Extruder Heatsink Fan.
M106 P1 C"Extruder Heatsink Fan" T55 S255 H1  		  ; Set the fan to full speed, but only after the extruder reaches 55c.
M950 F2 C"out4" Q25000                                ; Create fan 2 on pin out4 and set its frequency.
M106 P2 C"Electronics Fan" B0.1 L0.25 T35:60 H100     ; Set fan 2 name and value. Thermostatic control is turned on. Blip for 100ms. Set minimum speed to 1/4 of max, and start to turn on when the MCU hits 35c, then ramp up until it hits 60c.

; Tools
M563 P0 S"E3D V6" D0 H1 F0                            ; define tool 0
G10 P0 X0 Y0 Z0                                       ; set tool 0 axis offsets
G10 P0 R0 S0                                          ; set initial tool 0 active and standby temperatures to 0C
M290 Z-0.05											  ; Set babystepping to get that perfect first layer smoosh. Configure/disable this as needed.
M572 D0 S0.04										  ; Configure pressure advance. See https://marlinfw.org/tools/lin_advance/k-factor.html, then replace instances of "M900 K" to be "M572 D0 S".

; Miscellaneous
; M564 H0												  ; Move axes without homing
; M18 XYE												  ; Unlock the X, Y, and Extruder motors for manual movement
T0                                                    ; select first tool

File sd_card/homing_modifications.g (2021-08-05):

; tune motor drivers, set motor current and V parameter for homing moves

; apply modifications
M569 P0.4 V10          ; reduce V to ensure stealthChop is enabled for X
M569 P0.2 V10          ; reduce V to ensure stealthChop is enabled for Y
M913 X50 Y50 Z25       ; drop X and Y motor current to 50%, and Z to 25%
G4 P100                ; wait 100ms

; tune drivers
G91                      ; relative positioning
G1 H2 X0.2 Y0.2 F3000    ; power up motors to ensure they are not stalled
G4 P100                  ; wait 100ms
M400                     ; wait for current moves to finish

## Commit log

2021-06-09 Added first full set of customized stls
    [duplicator i3 duet controller case back panel.stl, duplicator i3 duet controller case cable lock.stl, duplicator i3 duet controller case chassis mount.stl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]
2021-06-13 Added some first draft psu mounts for the Meanwell LRS-350 power supply
    [duplicator i3 duet lrs 350 psu chassis mount.stl, duplicator i3 duet lrs 350 psu dock.stl]
2021-06-17 Added instructions for upgrading the printer to use a larger glass bed
    - Updated README to include the common Duplicator i3 upgrades I'm using
2021-06-22 Updated controller and psu mounts to now have the appropriate angle to hold their respective cases vertically
    [duplicator i3 duet controller case chassis mount.stl, duplicator i3 duet lrs 350 psu chassis mount.stl]
2021-06-25 First draft BOM added to README
2021-06-30 README BOM updates
2021-06-30 Updated README with fan adapter note
2021-07-02 Added meanwell 92mm psu fan stls
    [duplicator i3 duet lrs 350 psu 92mm fan case.stl, duplicator i3 duet lrs 350 psu 92mm fan clip.stl, duplicator i3 duet lrs 350 psu 92mm fan dock.stl]
2021-07-05 Repo reorganization
    - Divided PSU STLs into separate sub directories
    - Removed spaces from directory names
    - Moved 92mm meanwell PSU STLs into own folder in upgrades section
    - Updated 92mm Meanwell README to include a list of relvant STLs, and minor BOM update
    [duplicator i3 duet controller case back panel.stl, duplicator i3 duet controller case cable lock.stl, duplicator i3 duet controller case chassis mount.stl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]
2021-07-05 Updated the README tables to be properly formatted for easier editing
    - Added fan filters to core README BOM
2021-07-07 Updated README with idler pulley recommendation
2021-07-16 Updated 14 AWG wires to 12 AWG
    - Added #2 phillips to list of tools
2021-07-17 Added new part to BOM & fixed formatting
2021-07-18 Added an image of the almost complete 92mm fan case assembly
    - Updated quiet psu upgrade README
2021-07-18 Updated the quiet psu dock's external design to be slightly simpler
    [duplicator i3 duet lrs 350 psu dock.stl]
2021-07-18 Reorganized the repo's STL files
    - Updated the README with discrete sections that list the printable parts needed for each subassembly in the project
    [duplicator i3 duet controller case back panel.stl, duplicator i3 duet controller case cable lock.stl, duplicator i3 duet controller case chassis mount.stl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]
2021-07-21 README updates
    - Added notes about filament choice for components that'll be exposed to higher temperatures.
2021-07-21 Added additional required prusa stls to the extruder assemly
    - Updated README
    [prusa i3 mk2 extruder cover.stl, prusa i3 mk2 x carriage.stl]
2021-07-23 Added M3 square nuts to the BOM
2021-07-23 Updated stock psu mount to be angled properly for the frame rail
    [duplicator i3 duet stock psu chassis mount.stl]
2021-07-26 Built new duet case specific markdown file
2021-07-26 Built new extruder assembly markdown file
2021-07-26 Added a power supply markdown file
2021-07-26 Updated screwdriver section of duet case assembly markdown
2021-07-26 Added a basic x axis assembly readme
2021-07-26 Added basic y axis assembly readme
2021-07-26 Updated duet case BOM
2021-07-26 Updated extruder assembly BOM
2021-07-26 Updated power supply assembly BOM
2021-07-26 Updated x axis assembly BOM
2021-07-26 Updated y axis assembly BOM
2021-07-26 Cleaned up README to reflect assembly markdown changes
2021-07-26 Added another prusa STL to the extruder STLs
    [prusa i3 mk2 extruder idler.stl]
2021-07-26 Added extra whitespace to extruder_assembly.md
2021-07-26 Renamed drill instances to power drill
2021-07-26 Fixed table spacing for power drill changed
    - Updated zip tie BOM reference to be a bit cleaner
2021-07-27 Updated the borosilicate glass bed upgrade doc to be visually consistent with the other files
2021-07-27 Updated extruder assembly doc with another WIP STL
2021-07-27 Added some images
    - Updated the extruder assembly
2021-07-27 Tweaked extruder image pathing to main branch
2021-07-28 Updated y axis doc with additional required tools
2021-07-28 Updated STLs to be oriented properly
    [duplicator i3 duet controller case back panel.stl, duplicator i3 duet controller case cable lock.stl, duplicator i3 duet controller case chassis mount.stl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]
2021-07-28 Added rendered images to most of the assembly documents
2021-08-04 Added wiring diagram to README
2021-08-04 Updated wiring diagram README image to source from the main branch
2021-08-05 Updated wiring diagram illustrator file
2021-08-05 Added sd card files
    [bed.g, config.g, deployprobe.g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]
